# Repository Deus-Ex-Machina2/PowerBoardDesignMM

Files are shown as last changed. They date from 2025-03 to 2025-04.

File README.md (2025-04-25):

# Mircomouse Power Board Design
### Produced by: Rafael Cardoso and Amir Dollie 

This repository serves to hold and offer version control for the mircomouse power board designed.

**IMPORTANT:** since KiCAD, which was used to produce the necessary production files for submission to JLCPCB, does not allow easy merging capabilities for simultaneous development the following file strcuture was used:<br><br>

- Final Project Workfolder contains the final submission schematic and PCB: Final Project Workfolder -> Final
        (The other files in this section are for previous revision submissions and also contain images of JLCPCB quotes...etc)
- Raf'sWorkspace/MMPOwerBoardKiCAD9Version contains the most recent (current) schematic and pcb file for the entire PCB board.
- SchematicLibrary contains the files of all custom and imported symbols and footprints associated with the design.

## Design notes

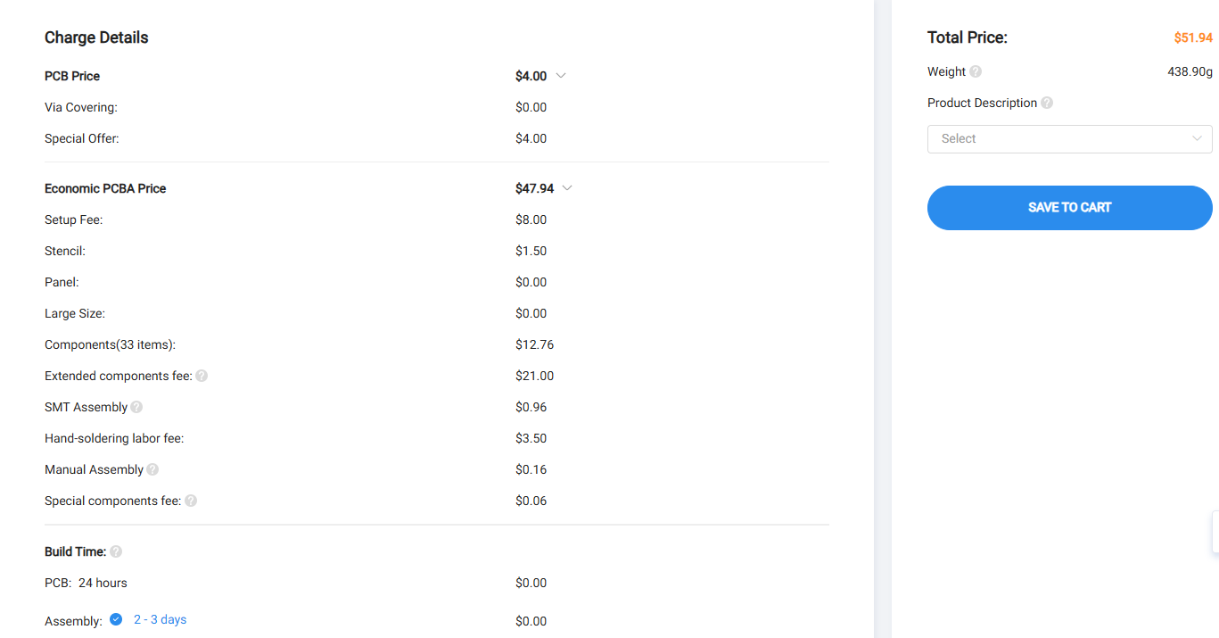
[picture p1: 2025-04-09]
Final Project Workfolder/Final/EEE3088F_Project_JLCPCBacceptance_CRDRAF001.png

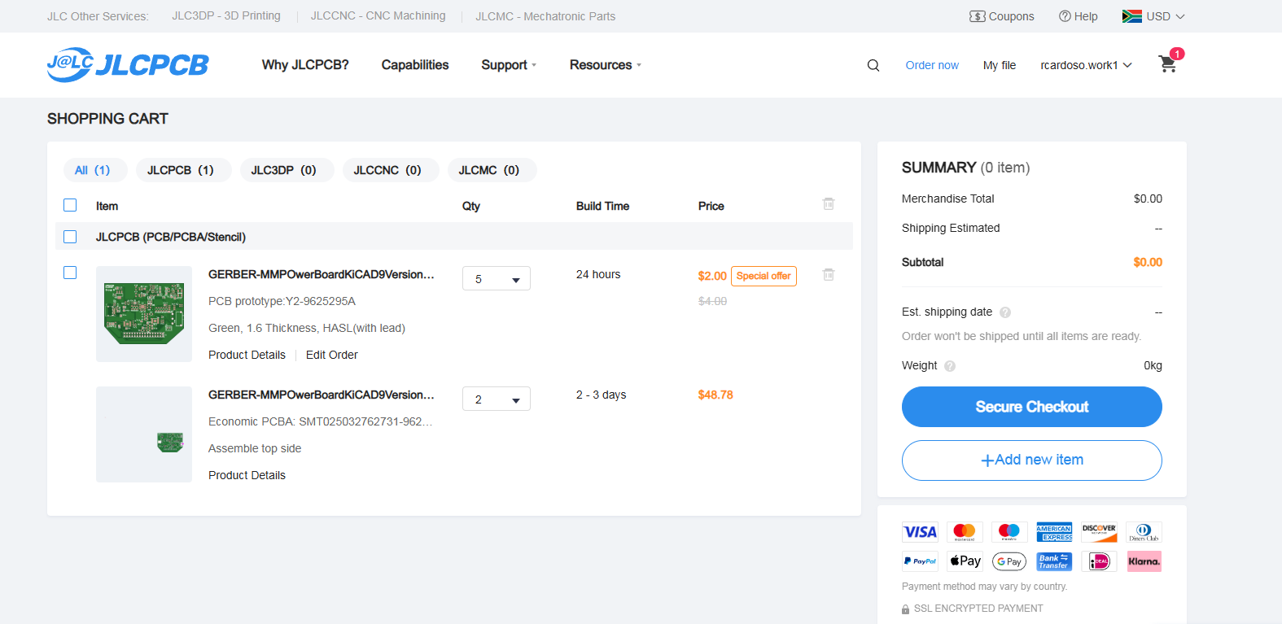
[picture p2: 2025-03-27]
Final Project Workfolder/JLCPCB_Quote2inCart.png

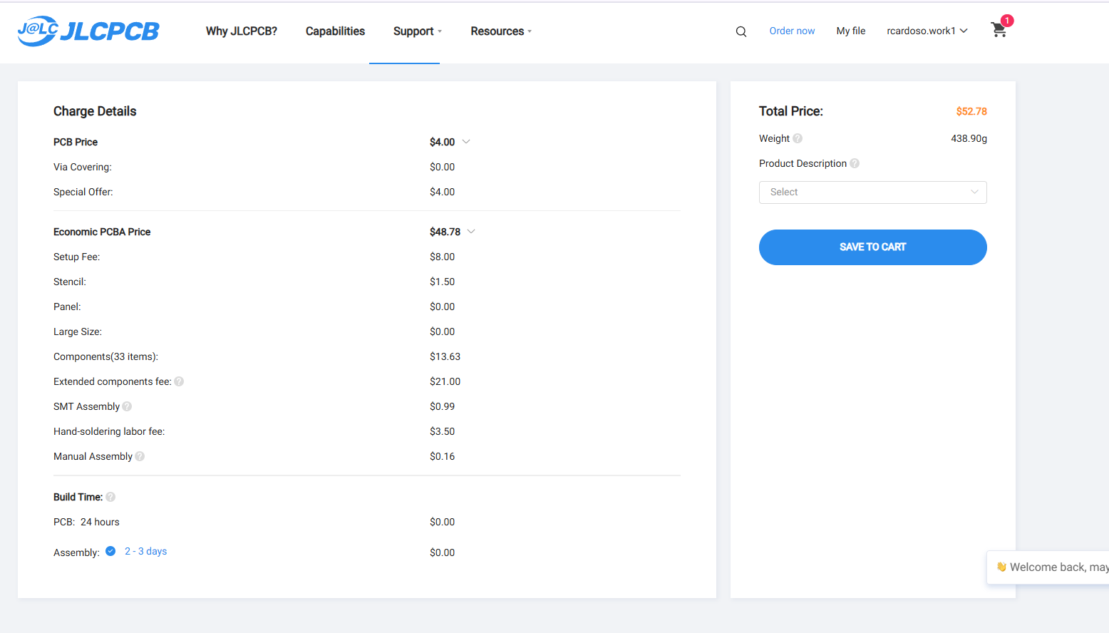
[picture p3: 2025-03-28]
Final Project Workfolder/(3)EEE3088F_Project_JLCPCBacceptance_CRDRAF001.png

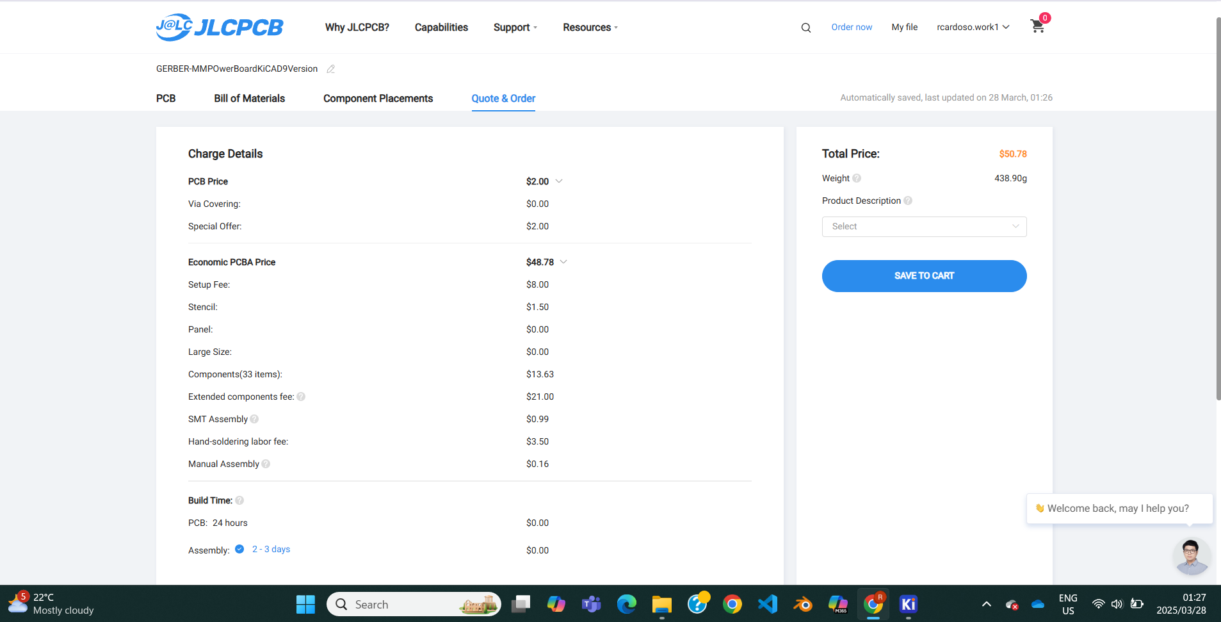
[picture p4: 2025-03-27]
Final Project Workfolder/(1)EEE3088F_Project_JLCPCBacceptance_CRDRAF001(1).png

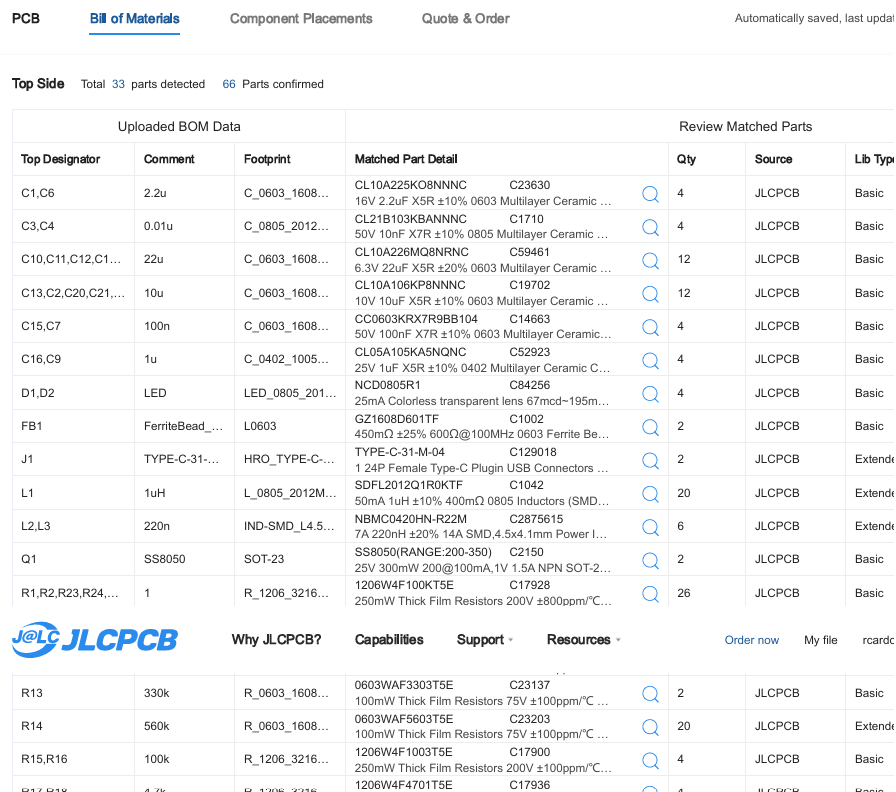
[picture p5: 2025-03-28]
Final Project Workfolder/(2)EEE3088F_Project_JLCPCBBOM_CRDRAF001.png

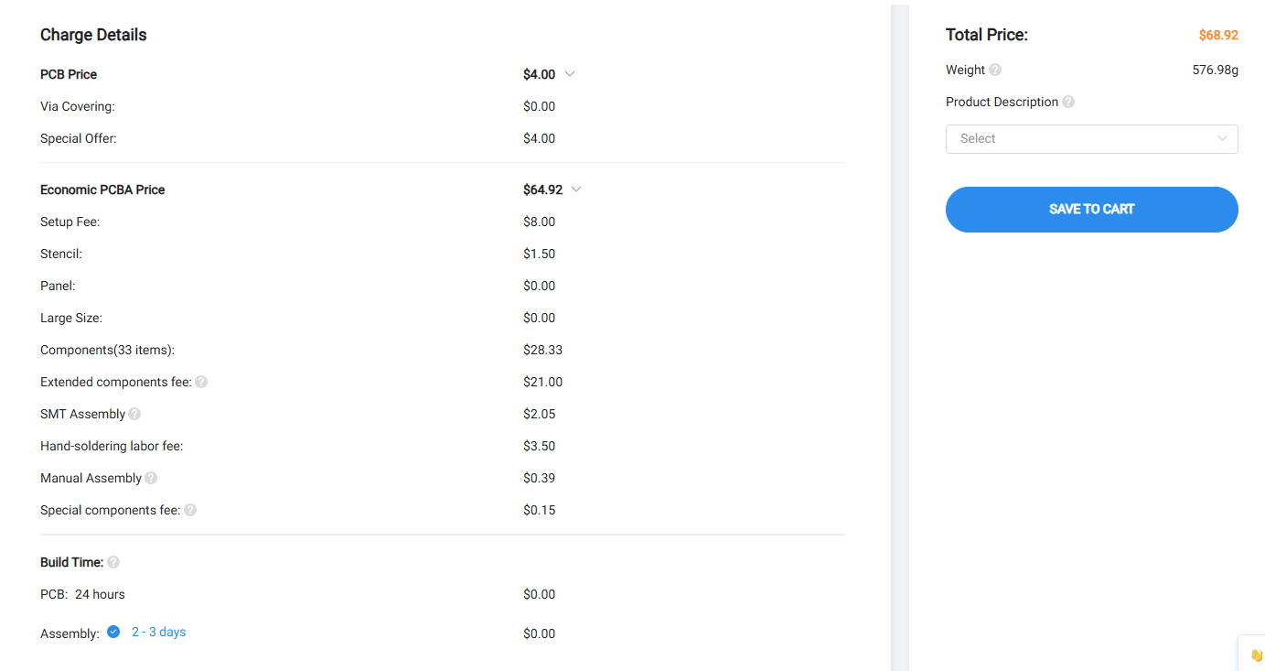
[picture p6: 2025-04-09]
Final Project Workfolder/Resubmit Budget Stuff Add to Cart Page.png

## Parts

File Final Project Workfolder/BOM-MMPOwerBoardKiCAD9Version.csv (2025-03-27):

Comment | Designator | Footprint | LCSC | Quantity
FerriteBead_Small | FB1 | L0603 | C1002 | 1
1uH | L1 | L_0805_2012Metric | C1042 | 1
TYPE-C-31-M-04 | J1 | HRO_TYPE-C-31-M-04 | C129018 | 1
TPS61236PRWLR | U6 | CONV_TPS61235PRWLR | C130295 | 1
INA219AIDR | U7 | SOIC127P599X175-8N | C138706 | 1
100n | C15,C7 | C_0603_1608Metric | C14663 | 2
TP4056-42-ESOP8 | U2 | SOIC127P600X175-9N | C16581 | 1
0.01u | C3,C4 | C_0805_2012Metric | C1710 | 2
SS-12D11-G050 | SW1 | SS-12D11-G050 | C17179528 | 1
75k | R19 | R_0805_2012Metric_Pad1.20x1.40mm_HandSolder | C17819 | 1
100k | R15,R16 | R_1206_3216Metric | C17900 | 2
1 | R1,R2,R23,R24,R3,R34,R35,R37,R4,R5,R6,R7,R8 | R_1206_3216Metric | C17928 | 13
4.7k | R17,R18 | R_1206_3216Metric | C17936 | 2
10u | C13,C2,C20,C21,C5,C8 | C_0603_1608Metric | C19702 | 6
SS8050 | Q1 | SOT-23 | C2150 | 1
HUSB237 | U1 | HUSB237-AA001DN06R- | C22373734 | 1
1M | R12,R20 | R_0603_1608Metric | C22935 | 2
330k | R13 | R_0603_1608Metric_Pad0.98x0.95mm_HandSolder | C23137 | 1
560k | R14 | R_0603_1608Metric_Pad0.98x0.95mm_HandSolder | C23203 | 1
2.2u | C1,C6 | C_0603_1608Metric | C23630 | 2
0.1 | R30,R31,R32,R33,R9 | R_1206_3216Metric | C25334 | 5
3.3k | R10,R11,R27 | R_0805_2012Metric | C26010 | 3
TPS22917DBVR | U10,U5 | SOT95P280X145-6N | C2681320 | 2
TPS63802DLAR | U4 | VREG_TPS63802DLAR | C2845237 | 1
220n | L2,L3 | IND-SMD_L4.5-W4.1_TMPA0402SP | C2875615 | 2
2.2k | R26,R36 | R_0603_1608Metric_Pad0.98x0.95mm_HandSolder | C4190 | 2
5.6k | R25 | R_0805_2012Metric | C4382 | 1
1k | R28,R29 | R_1206_3216Metric | C4410 | 2
DRV8833PWPR | U3,U9 | IC_DRV8833PWPR | C50506 | 2
1u | C16,C9 | C_0402_1005Metric | C52923 | 2
22u | C10,C11,C12,C14,C18,C19 | C_0603_1608Metric | C59461 | 6
AMS1117-5.0 | U11 | SOT-223_L6.5-W3.5-P2.30-LS7.0-BR | C6187 | 1
LED | D1,D2 | LED_0805_2012Metric | C84256 | 2

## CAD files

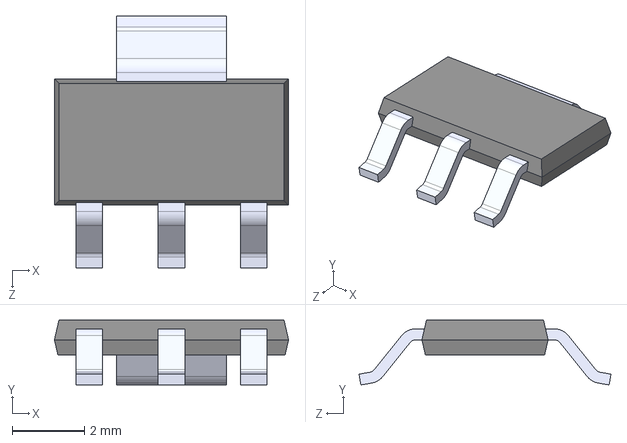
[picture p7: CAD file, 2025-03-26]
SchematicLibrary/AMS1117-5.0/AMS1117-5.0.step
6.50 x 1.80 x 7.00 mm

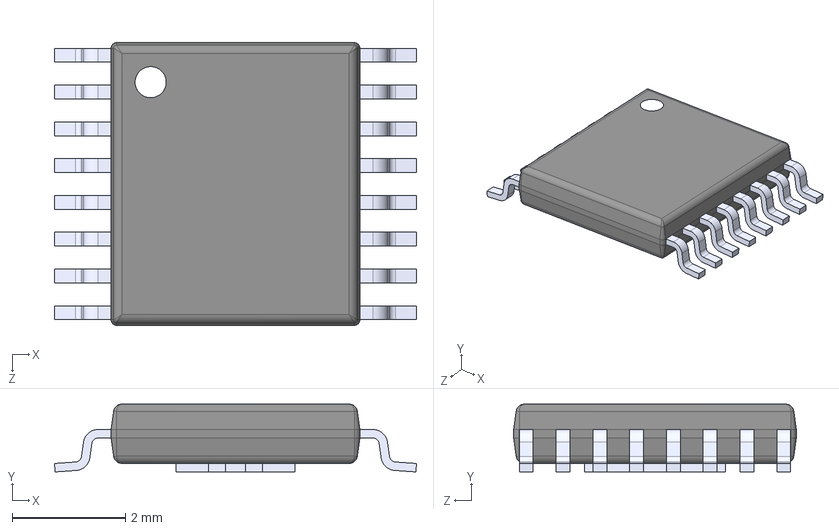
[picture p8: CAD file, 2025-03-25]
SchematicLibrary/DRV8833PWPR/DRV8833PWPR.step
6.40 x 1.20 x 5.00 mm

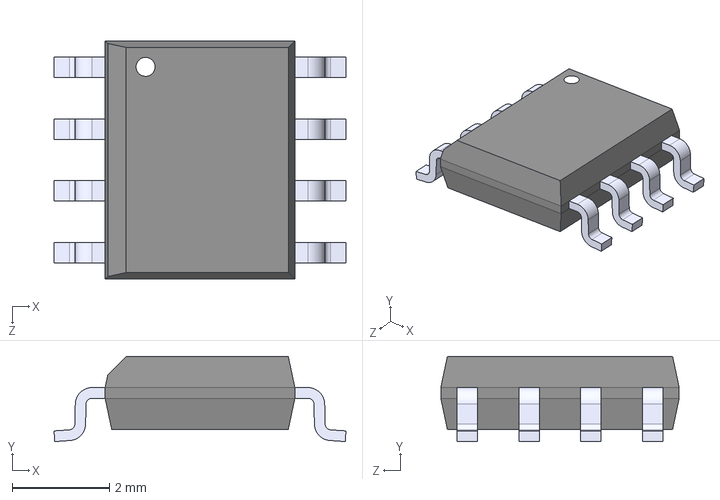
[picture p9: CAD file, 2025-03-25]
SchematicLibrary/INA219AIDR/INA219AIDR.step
6.00 x 1.75 x 4.90 mm

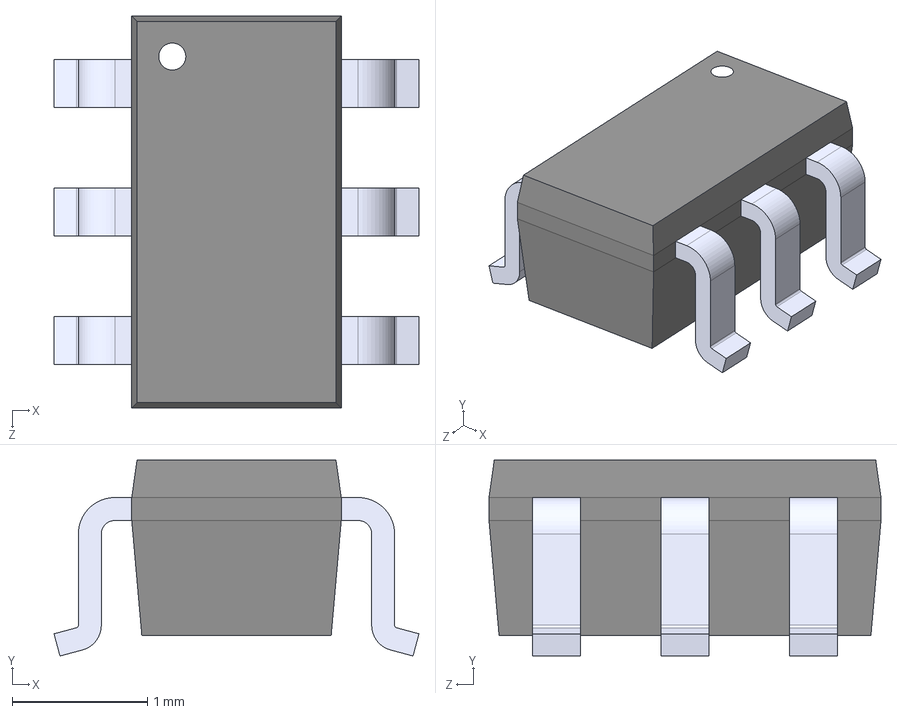
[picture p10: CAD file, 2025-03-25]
SchematicLibrary/MIC2005-1.2YM6-TR/MIC2005-1.2YM6-TR.step
2.70 x 1.45 x 2.90 mm

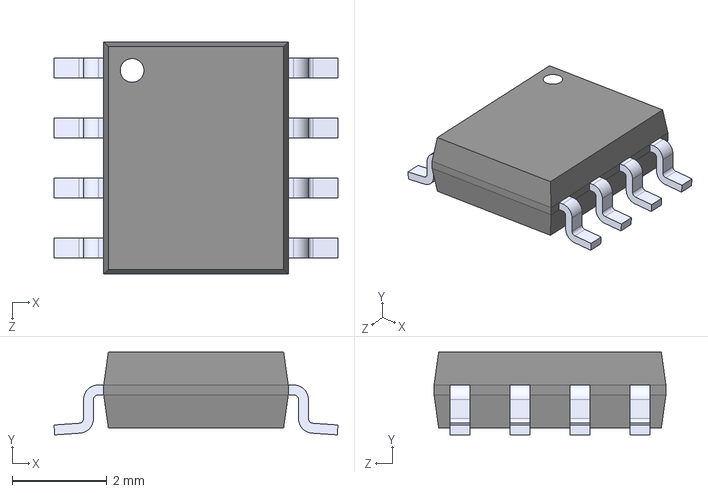
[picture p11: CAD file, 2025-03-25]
SchematicLibrary/TP4056-42-ESOP8/TP4056-42-ESOP8.step
6.00 x 1.75 x 4.90 mm

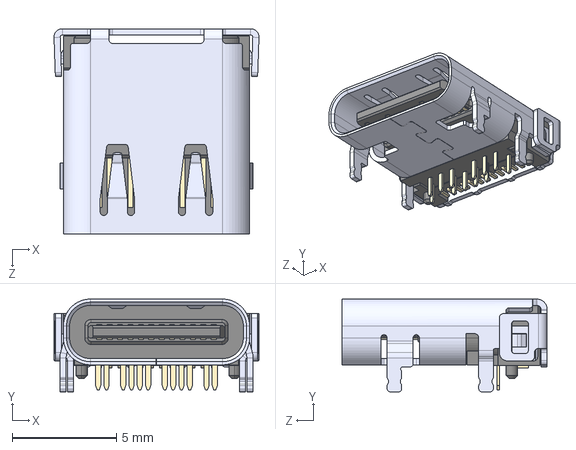
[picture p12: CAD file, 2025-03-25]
SchematicLibrary/TYPE-C-31-M-04/TYPE-C-31-M-04.step
9.85 x 4.46 x 9.87 mm

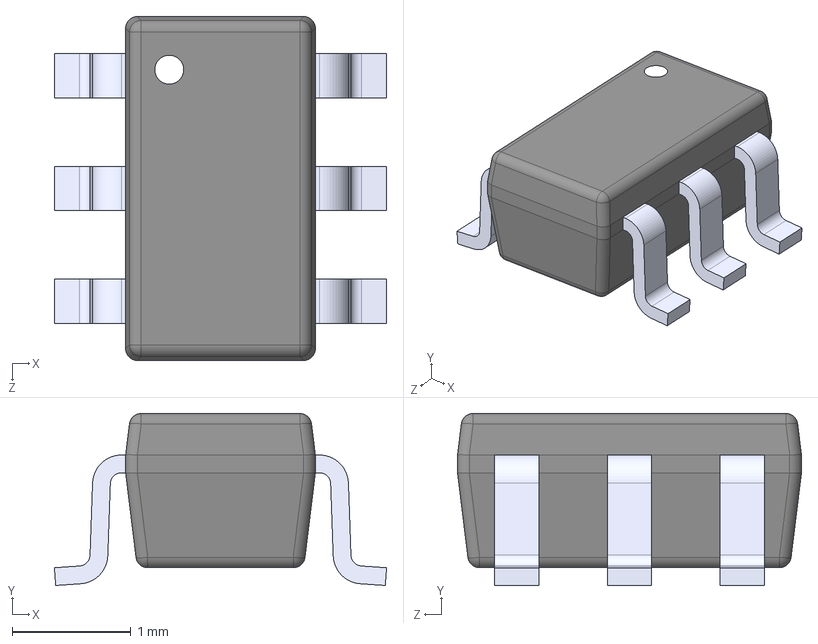
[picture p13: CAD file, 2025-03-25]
SchematicLibrary/TPS22917DBVR/TPS22917DBVR.step
2.80 x 1.45 x 2.90 mm

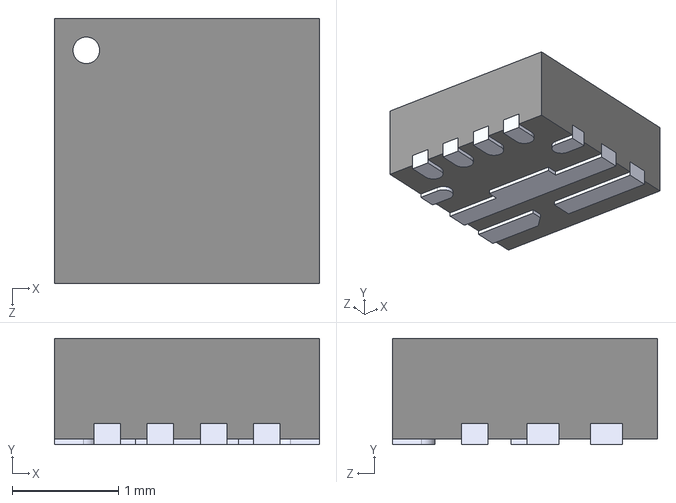
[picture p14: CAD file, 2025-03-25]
SchematicLibrary/TPS61236PRWLR/TPS61236PRWLR.step
2.50 x 1.00 x 2.50 mm

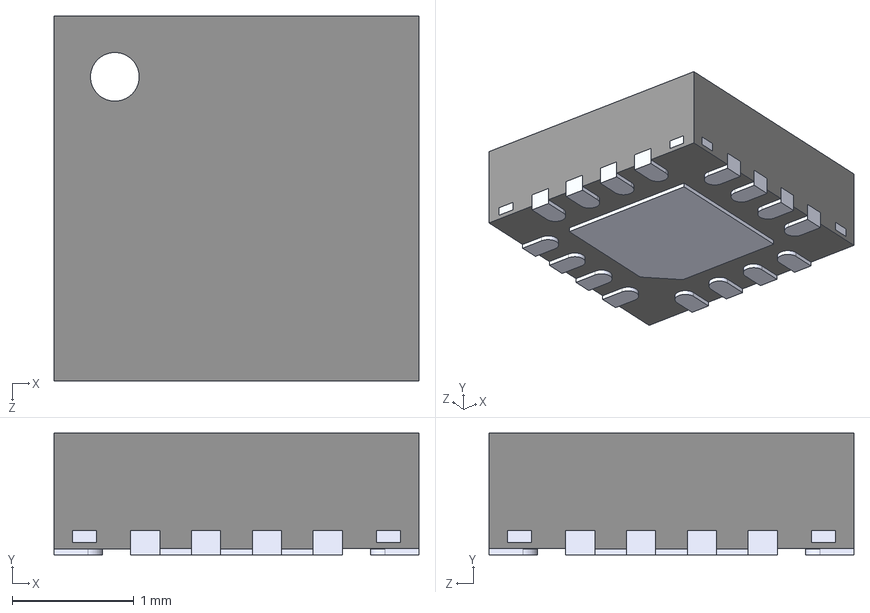
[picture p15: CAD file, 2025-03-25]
SchematicLibrary/TPS62133RGTR/TPS62133RGTR.step
3.00 x 1.00 x 3.00 mm

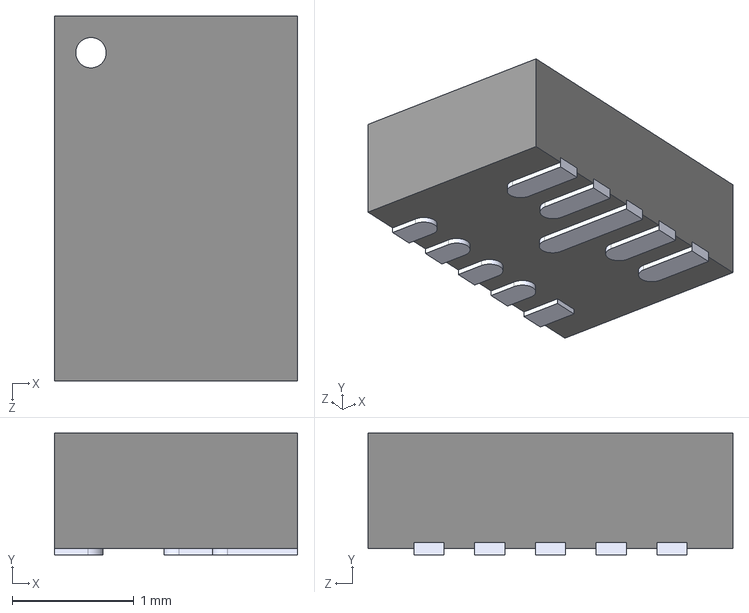
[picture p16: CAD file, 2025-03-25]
SchematicLibrary/TPS63802DLAR/TPS63802DLAR.step
2.00 x 1.00 x 3.00 mm

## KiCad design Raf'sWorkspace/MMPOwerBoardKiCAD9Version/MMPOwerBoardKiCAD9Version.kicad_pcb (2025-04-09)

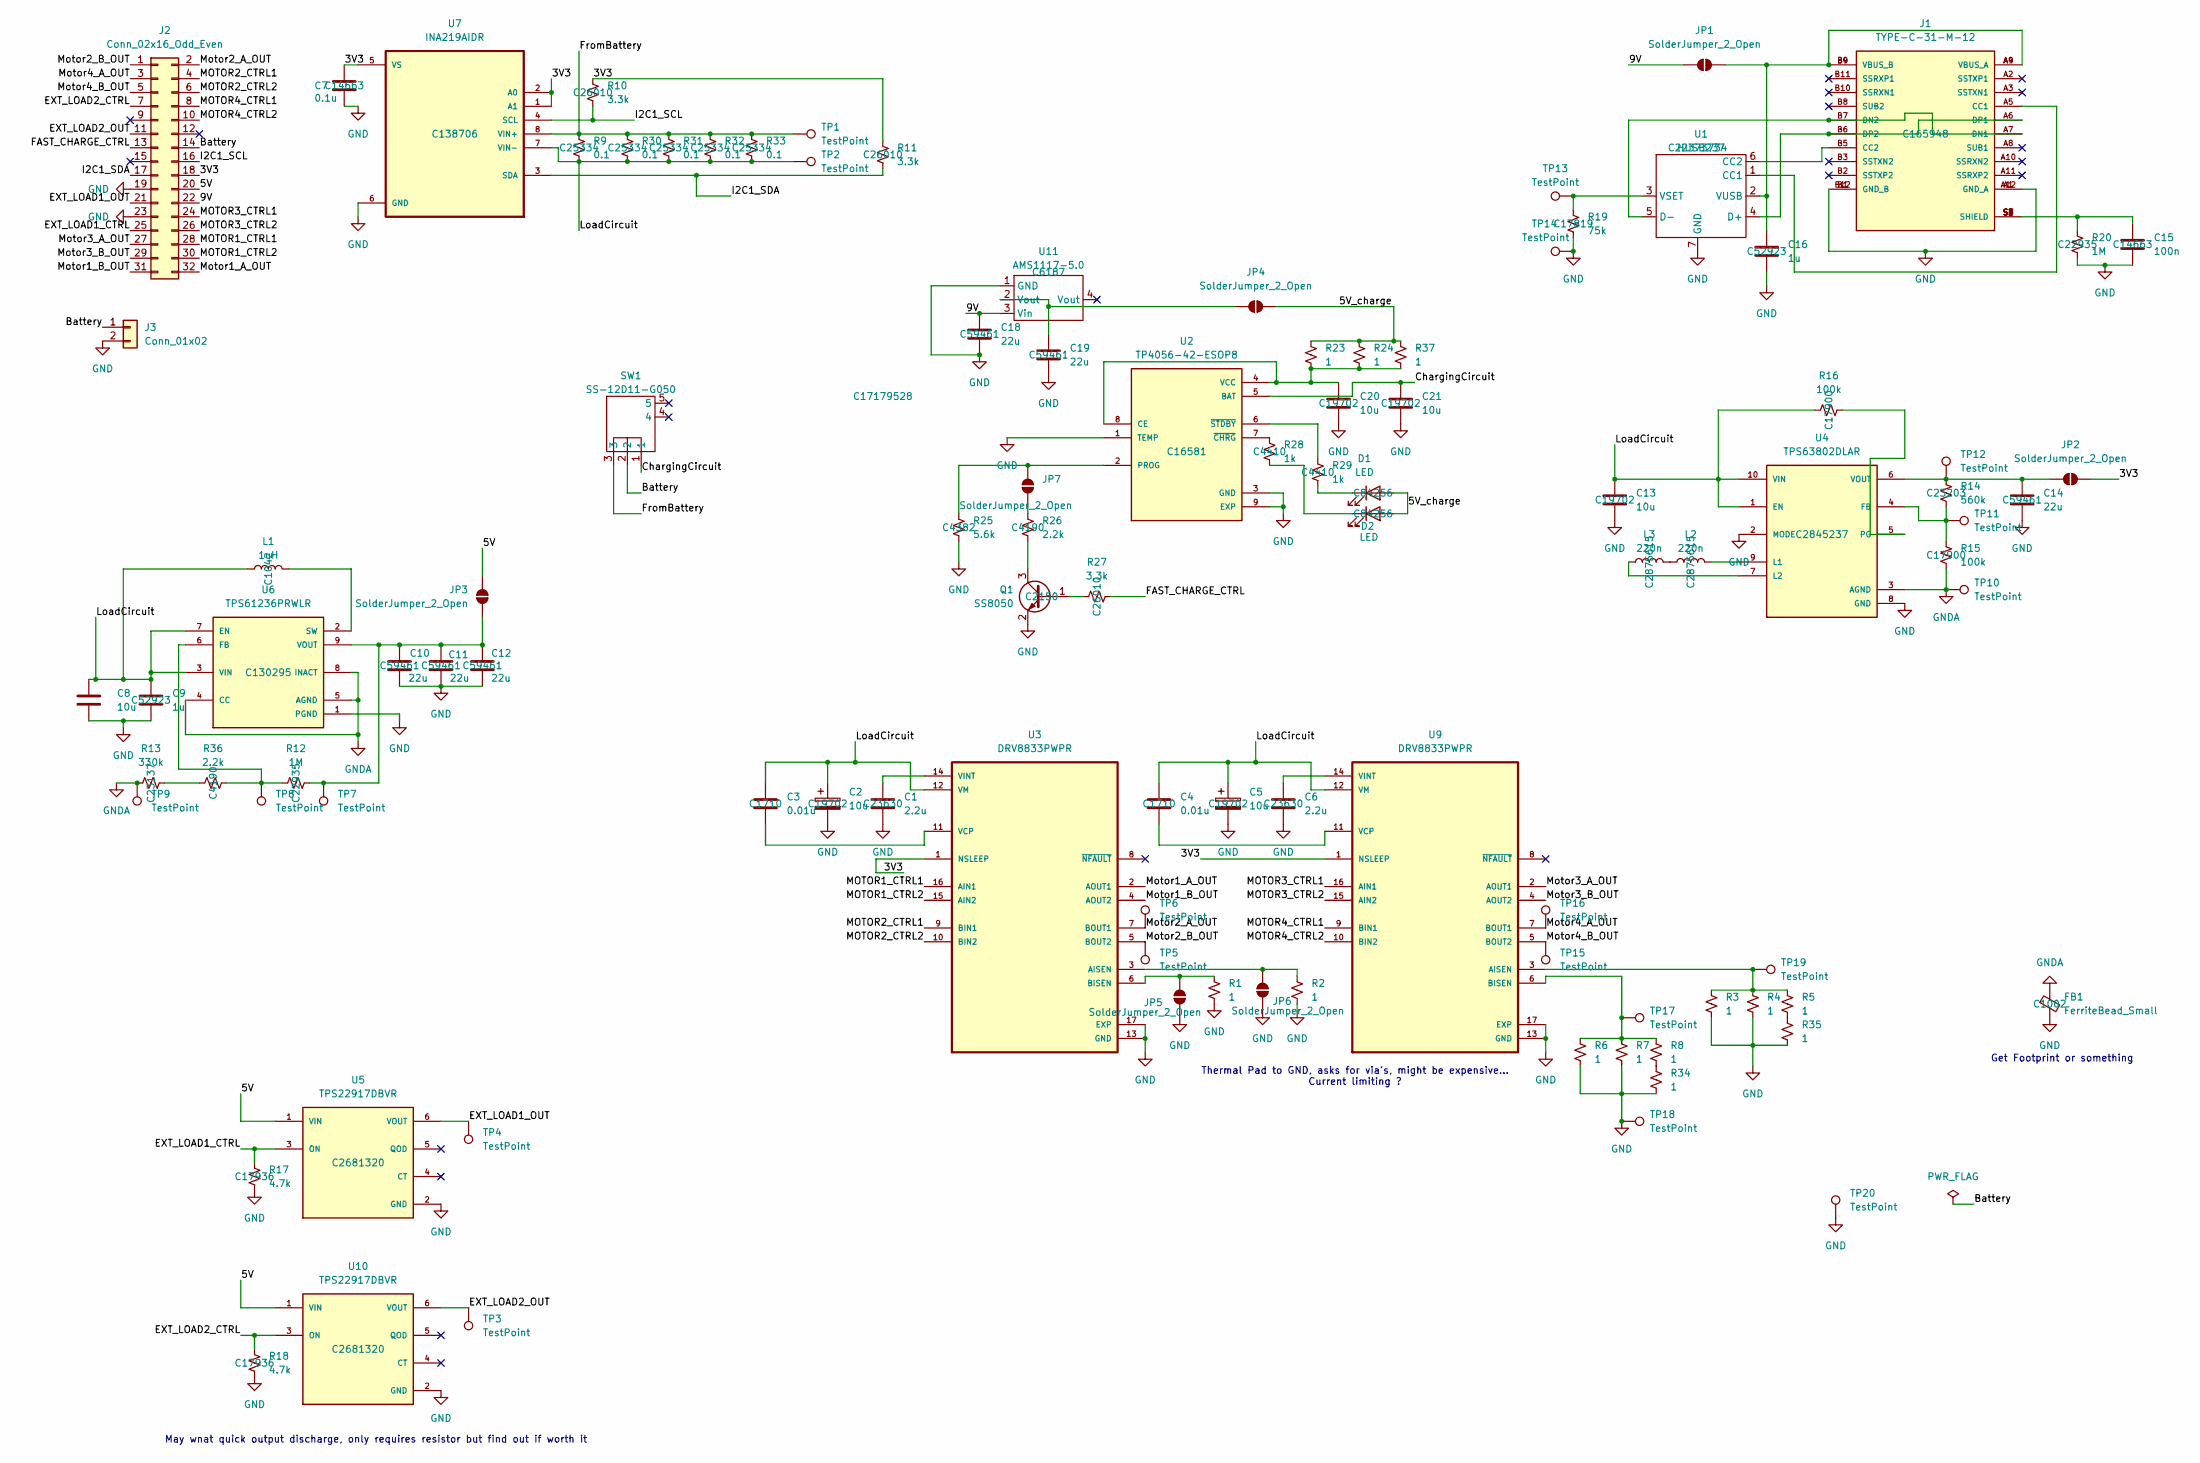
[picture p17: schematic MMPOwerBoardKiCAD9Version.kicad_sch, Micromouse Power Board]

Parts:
C1, C6: 2.2u; C_0603_1608Metric; LCSC C23630
C2, C5, C8, C13, C20, C21: 10u; C_0603_1608Metric; LCSC C19702
C3, C4: 0.01u; C_0805_2012Metric; LCSC C1710
C7: 0.1u; C_0603_1608Metric; LCSC C14663
C9, C16: 1u; C_0402_1005Metric; LCSC C52923
C10, C11, C12, C14, C18, C19: 22u; C_0603_1608Metric; LCSC C59461
C15: 100n; C_0603_1608Metric; LCSC C14663
D1, D2: LED; LED_0805_2012Metric; LCSC C84256
FB1: FerriteBead_Small; L0603; LCSC C1002
J1: TYPE-C-31-M-12; USB-C_SMD-TYPE-C-31-M-12; PARTREV A; LCSC C165948
J2: Conn_02x16_Odd_Even; PinHeader_2x16_P2.54mm_Vertical
J3: Conn_01x02; JST_PH_B2B-PH-K_1x02_P2.00mm_Vertical
JP1, JP2, JP3, JP4, JP5, JP6, JP7: SolderJumper_2_Open; SolderJumper-2_P1.3mm_Open_Pad1.0x1.5mm
L1: 1uH; L_0805_2012Metric; LCSC C1042
L2, L3: 220n; IND-SMD_L4.5-W4.1_TMPA0402SP; LCSC C2875615
Q1: SS8050; SOT-23; LCSC C2150
R1, R2, R3, R4, R5, R6, R7, R8, R23, R24, R34, R35, R37: 1; R_1206_3216Metric; LCSC C17928
R9, R30, R31, R32, R33: 0.1; R_1206_3216Metric; LCSC C25334
R10, R11: 3.3k; R_0805_2012Metric; LCSC C26010
R12, R20: 1M; R_0603_1608Metric; LCSC C22935
R13: 330k; R_0603_1608Metric_Pad0.98x0.95mm_HandSolder; LCSC C23137
R14: 560k; R_0603_1608Metric_Pad0.98x0.95mm_HandSolder; LCSC C23203
R15, R16: 100k; R_1206_3216Metric; LCSC C17900
R17, R18: 4.7k; R_1206_3216Metric; LCSC C17936
R19: 75k; R_0805_2012Metric_Pad1.20x1.40mm_HandSolder; LCSC C17819
R25: 5.6k; R_0805_2012Metric; LCSC C4382
R26: 2.2k; R_0603_1608Metric_Pad0.98x0.95mm_HandSolder; LCSC C4190
R27: 3.3k; R_0805_2012Metric_Pad1.20x1.40mm_HandSolder; LCSC C26010
R28, R29: 1k; R_1206_3216Metric; LCSC C4410
R36: 2.2k; R_0603_1608Metric; LCSC C4190
SW1: SS-12D11-G050; LCSC C17179528
TP1, TP2, TP3, TP4, TP5, TP6, TP7, TP8, TP9, TP10, TP11, TP12, TP13, TP14, TP15, TP16, TP17, TP18, TP19: TestPoint; TestPoint_Pad_1.5x1.5mm
TP20: TestPoint; TestPoint_Pad_4.0x4.0mm
U1: HUSB237; HUSB237-AA001DN06R-; LCSC C22373734
U2: TP4056-42-ESOP8; SOIC127P600X175-9N; PARTREV NA; LCSC C16581
U3, U9: DRV8833PWPR; HTSSOP-16-1EP_4.4x5mm_P0.65mm_EP3.4x5mm; PARTREV E; LCSC C50506
U4: TPS63802DLAR; VREG_TPS63802DLAR; PARTREV B; LCSC C2845237
U5, U10: TPS22917DBVR; SOT95P280X145-6N; PARTREV B; LCSC C2681320
U6: TPS61236PRWLR; CONV_TPS61235PRWLR; LCSC C130295
U7: INA219AIDR; SOIC127P599X175-8N; LCSC C138706
U11: AMS1117-5.0; SOT-223_L6.5-W3.5-P2.30-LS7.0-BR; LCSC C6187

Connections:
/3V3: C7.1, J2.18, JP2.2 (B), R10.1, R11.1, U3.1 (NSLEEP), U7.1 (A1), U7.2 (A0), U7.5 (VS), U9.1 (NSLEEP)
/5V: J2.20, JP3.1 (A), U5.1 (VIN), U10.1 (VIN)
/5V_charge: D1.2 (A), D2.2 (A), JP4.2 (B), R23.1, R24.1, R37.1
/9V: C18.1, J2.22, JP1.1 (A), U11.3 (Vin)
/Battery: J2.14, J3.1, SW1.2
/ChargingCircuit: C21.1, SW1.1, U2.5 (BAT)
/EXT_LOAD1_CTRL: J2.25, R17.1, U5.3 (ON)
/EXT_LOAD1_OUT: J2.21, TP4.1, U5.6 (VOUT)
/EXT_LOAD2_CTRL: J2.7, R18.1, U10.3 (ON)
/EXT_LOAD2_OUT: J2.11, TP3.1, U10.6 (VOUT)
/FAST_CHARGE_CTRL: J2.13, R27.1
/FromBattery: R9.1, R30.1, R31.1, R32.1, R33.1, SW1.3, TP1.1, U7.8 (VIN+)
/I2C1_SCL: J2.16, R10.2, U7.4 (SCL)
/I2C1_SDA: J2.17, R11.2, U7.3 (SDA)
/LoadCircuit: C2.1, C3.1, C4.1, C5.1, C8.1, C9.1, C13.1, L1.1, R9.2, R16.1, R30.2, R31.2, R32.2, R33.2, TP2.1, U3.12 (VM), U4.1 (EN), U4.10 (VIN), U6.3 (VIN), U6.7 (EN), U7.7 (VIN-), U9.12 (VM)
/MOTOR1_CTRL1: J2.28, U3.16 (AIN1)
/MOTOR1_CTRL2: J2.30, U3.15 (AIN2)
/MOTOR2_CTRL1: J2.4, U3.9 (BIN1)
/MOTOR2_CTRL2: J2.6, U3.10 (BIN2)
/MOTOR3_CTRL1: J2.24, U9.16 (AIN1)
/MOTOR3_CTRL2: J2.26, U9.15 (AIN2)
/MOTOR4_CTRL1: J2.8, U9.9 (BIN1)
/MOTOR4_CTRL2: J2.10, U9.10 (BIN2)
/Motor1_A_OUT: J2.32, U3.2 (AOUT1)
/Motor1_B_OUT: J2.31, U3.4 (AOUT2)
/Motor2_A_OUT: J2.2, TP6.1, U3.7 (BOUT1)
/Motor2_B_OUT: J2.1, TP5.1, U3.5 (BOUT2)
/Motor3_A_OUT: J2.27, U9.2 (AOUT1)
/Motor3_B_OUT: J2.29, U9.4 (AOUT2)
/Motor4_A_OUT: J2.3, TP16.1, U9.7 (BOUT1)
/Motor4_B_OUT: J2.5, TP15.1, U9.5 (BOUT2)
GND: C1.2, C2.2, C5.2, C6.2, C7.2, C8.2, C9.2, C10.2, C11.2, C12.2, C13.2, C14.2, C15.2, C16.2, C18.2, C19.2, C20.2, C21.2, FB1.2, J1.A1 (GND_A), J1.A12 (GND_A), J1.B1 (GND_B), J1.B12 (GND_B), J2.19, J2.23, J3.2, JP5.2 (B), JP6.2 (B), Q1.2 (E), R1.2, R2.2, R3.2, R4.2, R6.2, R7.2, R17.2, R18.2, R19.2, R20.2, R25.1, R34.2, R35.2, TP14.1, TP18.1, TP20.1, U1.7 (GND), U2.1 (TEMP), U2.3 (GND), U2.9 (EXP), U3.13 (GND), U3.17 (EXP), U4.2 (MODE), U4.8 (GND), U5.2 (GND), U6.1 (PGND), U7.6 (GND), U9.13 (GND), U9.17 (EXP), U10.2 (GND), U11.1 (GND)
GNDA: FB1.1, R13.1, R15.2, TP9.1, TP10.1, U4.3 (AGND), U6.4 (CC), U6.5 (AGND), U6.8 (INACT)
unnamed: C15.1, J1.S1 (SHIELD), J1.S2 (SHIELD), J1.S3 (SHIELD), J1.S4 (SHIELD), J1.S5 (SHIELD), J1.S6 (SHIELD), J1.S7 (SHIELD), J1.S8 (SHIELD), R20.1
unnamed: D1.1 (K), R29.1
unnamed: D2.1 (K), R28.1
unnamed: J1.A5 (CC1), U1.1 (CC1)
unnamed: J1.B5 (CC2), U1.6 (CC2)
unnamed: J1.A7 (DN1), J1.B7 (DN2), U1.5 (D-)
unnamed: J1.A6 (DP1), J1.B6 (DP2), U1.4 (D+)
unnamed: C16.1, J1.A4 (VBUS_A), J1.A9 (VBUS_A), J1.B4 (VBUS_B), J1.B9 (VBUS_B), JP1.2 (B), U1.2 (VUSB)
unnamed: C14.1, JP2.1 (A), R14.1, TP12.1, U4.6 (VOUT)
unnamed: C10.1, C11.1, C12.1, JP3.2 (B), R12.2, TP7.1, U6.9 (VOUT)
unnamed: C19.1, JP4.1 (A), U11.2 (Vout)
unnamed: JP5.1 (A), R1.1, U3.6 (BISEN)
unnamed: JP6.1 (A), R2.1, U3.3 (AISEN)
unnamed: JP7.1 (A), R26.2
unnamed: JP7.2 (B), R25.2, U2.2 (PROG)
unnamed: L2.1, L3.2
unnamed: Q1.1 (B), R27.2
unnamed: Q1.3 (C), R26.1
unnamed: R13.2, R36.1
unnamed: R8.2, R34.1
unnamed: R5.2, R35.1
unnamed: R19.1, TP13.1, U1.3 (VSET)
unnamed: C20.1, R23.2, R24.2, R37.2, U2.4 (VCC), U2.8 (CE)
unnamed: R28.2, U2.7 (~CHRG)
unnamed: R29.2, U2.6 (~STDBY)
unnamed: C3.2, U3.11 (VCP)
unnamed: C1.1, U3.14 (VINT)
unnamed: R14.2, R15.1, TP11.1, U4.4 (FB)
unnamed: L2.2, U4.9 (L1)
unnamed: L3.1, U4.7 (L2)
unnamed: R16.2, U4.5 (PG)
unnamed: R12.1, R36.2, TP8.1, U6.6 (FB)
unnamed: L1.2, U6.2 (SW)
unnamed: R3.1, R4.1, R5.1, TP19.1, U9.3 (AISEN)
unnamed: R6.1, R7.1, R8.1, TP17.1, U9.6 (BISEN)
unnamed: C4.2, U9.11 (VCP)
unnamed: C6.1, U9.14 (VINT)

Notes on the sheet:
Get Footprint or something
Thermal Pad to GND, asks for via's, might be expensive... Current limiting ?
May wnat quick output discharge, only requires resistor but find out if worth it

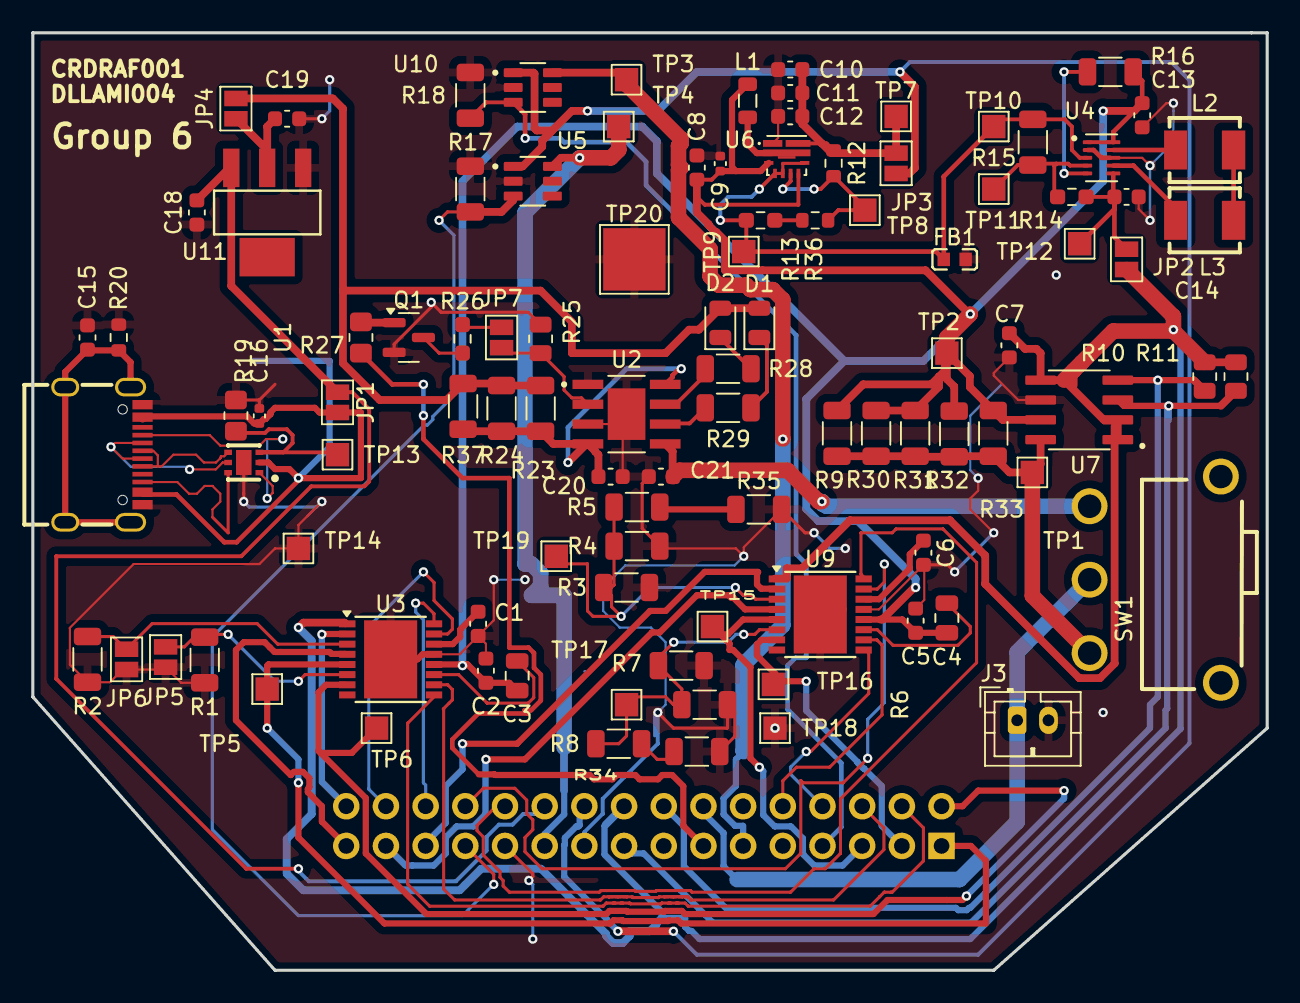
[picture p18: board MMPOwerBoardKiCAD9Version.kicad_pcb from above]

Board: 2 copper layers, 79.0 x 60.0 mm, 103 parts (1 on the bottom side), 70 nets.

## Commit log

2025-03-25 Added Librarby for most chosen components footprint and schematics
    [MMPowerBoard.kicad_pcb, MMPowerBoard.kicad_sch, TP4056-42-ESOP8.step]
2025-03-25 Added to library and updated schematic in Raf Work folder
    [DRV8833PWPR.step, INA219AIDR.step, MIC2005-1.2YM6-TR.step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]
2025-03-26 Added a few things to schematic and added new LDO schematic to library
    [AMS1117-5.0.step, MMPOwerBoardKiCAD9Version.kicad_sch, TPS61236PRWLR.step]
2025-03-26 Almost complete schematic
    [MMPOwerBoardKiCAD9Version.kicad_sch]
2025-03-27 Final Schematic complete with test points and jumpers
    [MMPOwerBoardKiCAD9Version.kicad_sch]
2025-03-27 Added BOM and PCB and LCSC numbers, Schematic complete
    [BOM-MMPOwerBoardKiCAD9Version.csv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]
2025-03-27 Organised PCB on recommended board size
    [MMPOwerBoardKiCAD9Version.kicad_pcb, MMPOwerBoardKiCAD9Version.kicad_sch]
2025-03-27 Added wiring of the PCB with Free-router
2025-03-27 Revert "Added wiring of the PCB with Free-router"
    This reverts commit c34e8a51645d4334bd9fe00579e44e527089207a.
2025-03-27 Added all tracks
    [MMPOwerBoardKiCAD9Version.kicad_pcb, MMPOwerBoardKiCAD9Version.kicad_sch]
2025-03-27 PCB seems to be done - BOM also generated
    [BOM-MMPOwerBoardKiCAD9Version.csv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]
2025-03-27 GTFO Finished
    [BOM-MMPOwerBoardKiCAD9Version.csv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]
2025-03-28 A few minor changes to improve results on rule checker: 0,1mm adjusted to 0,15mm, regions of silkscreen on pad were removed
    [CPL-MMPOwerBoardKiCAD9Version.csv, MMPOwerBoardKiCAD9Version-CuBottom.gbr, MMPOwerBoardKiCAD9Version-CuTop.gbr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]
2025-03-28 Added Drill hole space x1 to hold up board
    [CPL-MMPOwerBoardKiCAD9Version.csv, MMPOwerBoardKiCAD9Version-CuBottom.gbr, MMPOwerBoardKiCAD9Version-CuTop.gbr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]
2025-04-09 Made changes to hole sizes, minimum track width stuff (1.5mm) and other compliance things
    [CPL-MMPOwerBoardKiCAD9Version.csv, MMPOwerBoardKiCAD9Version-CuBottom.gbr, MMPOwerBoardKiCAD9Version-CuTop.gbr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]
2025-04-09 Changed the USB-C connector, and connected it - removed Ground layers, changed silkscreens for a few units
    [MMPOwerBoardKiCAD9Version.kicad_pcb, MMPOwerBoardKiCAD9Version.kicad_sch]
2025-04-09 Fixed PCB board, DRC has 0 errors now apparently
    [BOM-MMPOwerBoardKiCAD9Version.csv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]
2025-04-09 Added the JLC PCB submission pcis and stuff [named incorrectedly
    [BOM-MMPOwerBoardKiCAD9Version.csv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]
2025-04-09 Final files for resubmit attached in Final Workspace-> Final
    [BOM-MMPOwerBoardKiCAD9Version.csv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]
